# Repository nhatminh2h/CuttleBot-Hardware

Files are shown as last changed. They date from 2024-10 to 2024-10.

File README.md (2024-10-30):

# CuttleBot and FOLD Actuator Electronics Design
This repository contains the electronics design files and firmware for the CuttleBot, a biomimetic underwater robot, and its FOLD actuators. The system architecture is designed for efficient control and feedback, providing precise manipulation of the actuators for underwater mobility.

A follow up work from [Fin ray-inspired, Origami, Small Scale Actuator for Fin Manipulation in Aquatic Bioinspired Robots](https://arxiv.org/abs/2407.16821)

---

## System Overview

The CuttleBot's electronic system is divided into two key components:
1. **Main Controller**
2. **Driver and Actuator Modules (8 units)**

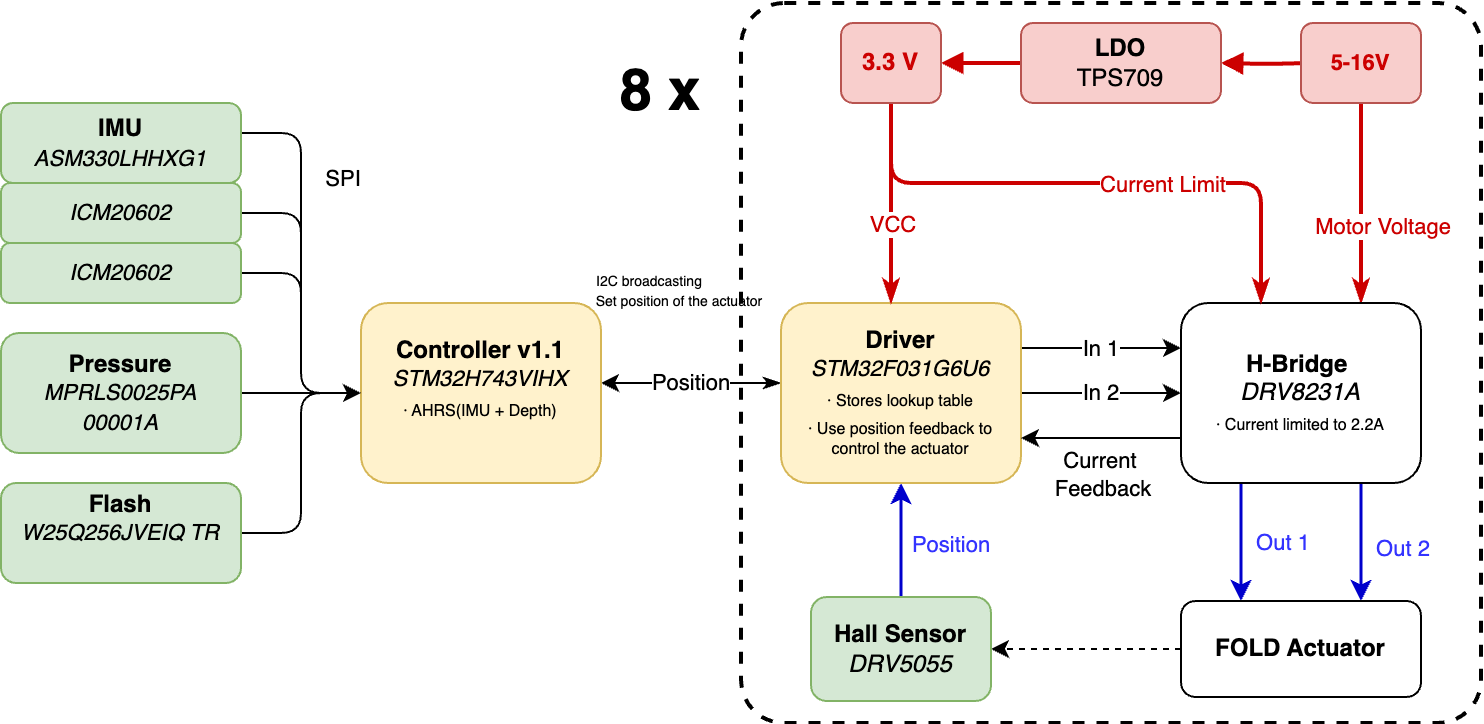
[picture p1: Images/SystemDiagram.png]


---

## Components

### Main Controller (Current version: v1.1)

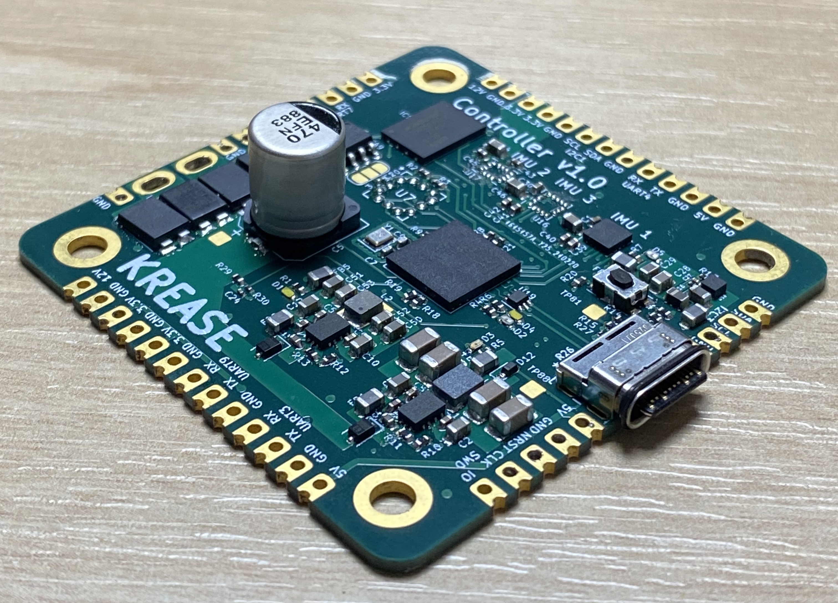
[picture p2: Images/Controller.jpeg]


- **Microcontroller**: STM32H743VHX
- **Connected Sensors**:
  - **IMU**: Three sensors (ASM330LHHXG1, ICM20602, ICM20602) are connected over SPI to provide Attitude and Heading Reference System (AHRS) data for underwater navigation.
  - **Pressure Sensor**: MPRLS0025PA 00001A, used to determine depth.
  - **Flash Memory**: W25Q256/VEIQ TR, for data storage.

The main controller (STM32H743VHX) processes data from the IMUs and the pressure sensor to calculate the robot's position and orientation. It then broadcasts the actuator position setpoints over I2C to each of the driver modules.

### Driver Module (8 units)

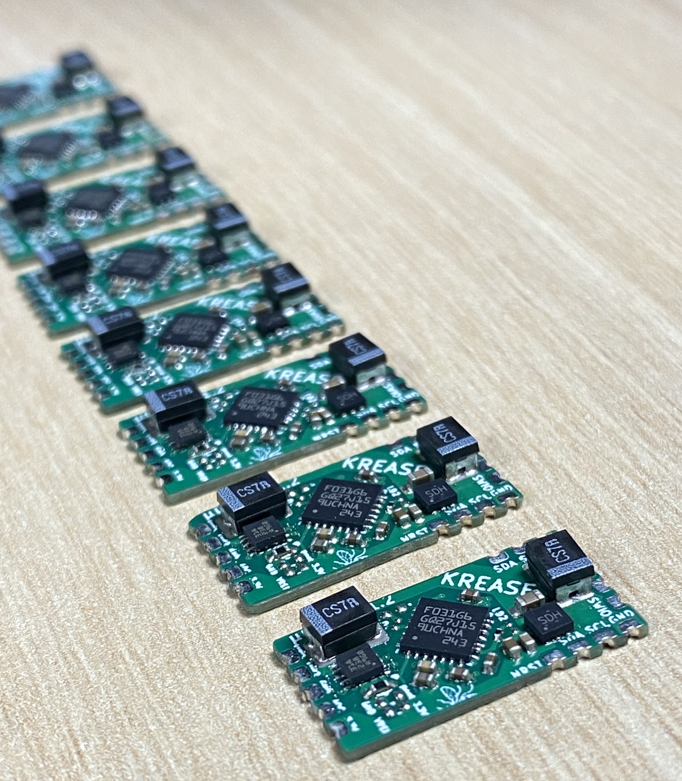
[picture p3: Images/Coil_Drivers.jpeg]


Each FOLD actuator has its own dedicated driver module, responsible for controlling the actuator's motion and maintaining position feedback. The driver module is built around the following components:

- **Microcontroller**: STM32F031G6U6
  - Stores lookup tables for position control and uses feedback from the Hall sensor to control actuator position.
  
- **Hall Sensor**: DRV5055
  - Provides position feedback to the driver, enabling precise control of actuator movement.

- **Motor Driver (H-Bridge)**: DRV8231A
  - Drives the actuator with current limiting up to 2.2A, allowing bidirectional motor control.
  - Receives control signals from the driver microcontroller.

- **Voltage Regulation**: 
  - **LDO (TPS709)** provides a stable 3.3V supply for the driver microcontroller and Hall sensor.
  - Supports a motor voltage range of 5-16V for the H-Bridge.

#### FOLD Actuator

The FOLD actuator is an origami-inspired, electromagnetically driven, tendon-driven actuator. Controlled via the H-Bridge and regulated by position feedback from the Hall sensor, the actuator provides precise biomimetic movement for underwater mobility.

---

### Power and Communication

- **Power**:
  - Each driver module includes an LDO (TPS709) to provide a stable 3.3V for the microcontroller and sensor circuits.
  - The motor voltage can range from 5-16V, which also powers the H-Bridge for actuator control.
  
- **Communication**:
  - **I2C** is used by the main controller to broadcast actuator position setpoints to each driver module.
  - **SPI** communication links the main controller to the IMUs, pressure sensor, and flash memory.

---

### Getting Started

1. **Cloning the Repository**:
   ```bash
   git clone https://github.com/[username]/cuttlebot-electronics.git

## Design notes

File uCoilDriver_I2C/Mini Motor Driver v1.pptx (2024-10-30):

## Mini Motor Driver v1.0 – Overview

- Nominal input voltage: 5-18V

Gus Zhang <cheng.zhang@manchester.ac.uk> , Aug 2023

Connector pitch: 1.27 mm

Left Connector (FPC)
Motor Drive Out 1
Motor Drive Out 2
GND – Hall Sensor
+3V3 – Hall Sensor
Out – Hall Sensor

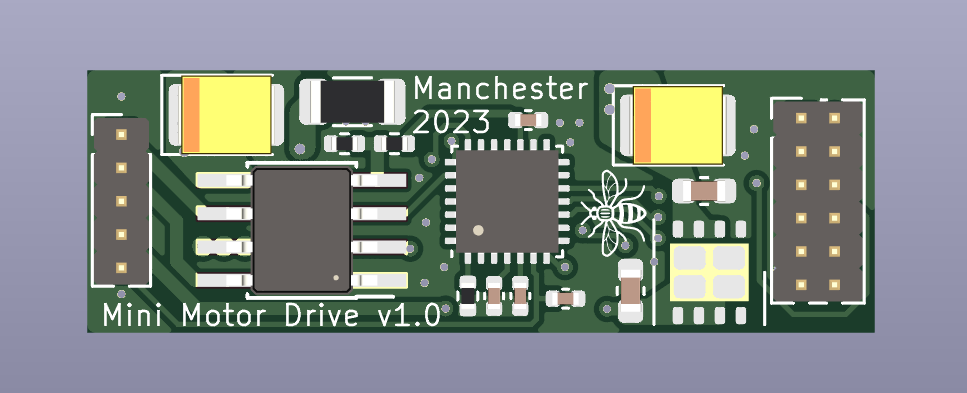
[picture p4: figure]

3cm

Right Connector (MB)
+12V | +12V
GND | GND
SPI_MOSI | UART_TX
SPI_SCK | UART_RX
SPI_NSS | SWDIO
NRST | SWCLK

1cm

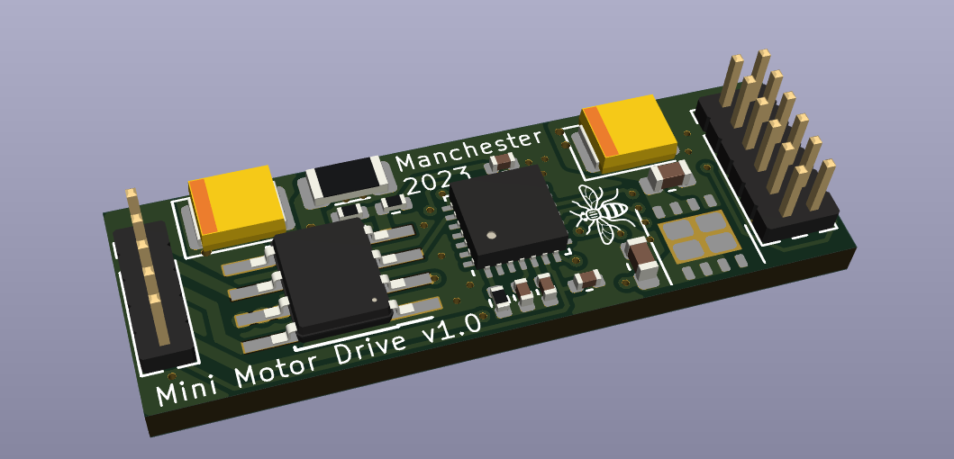
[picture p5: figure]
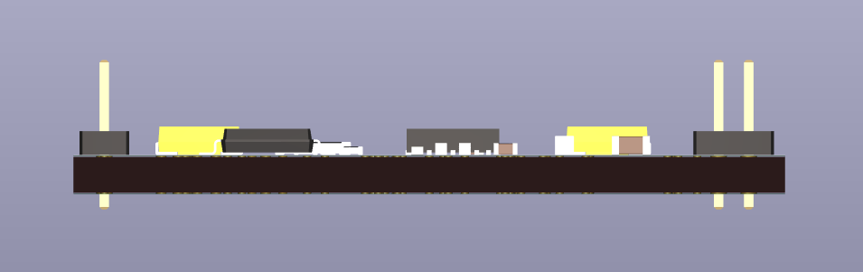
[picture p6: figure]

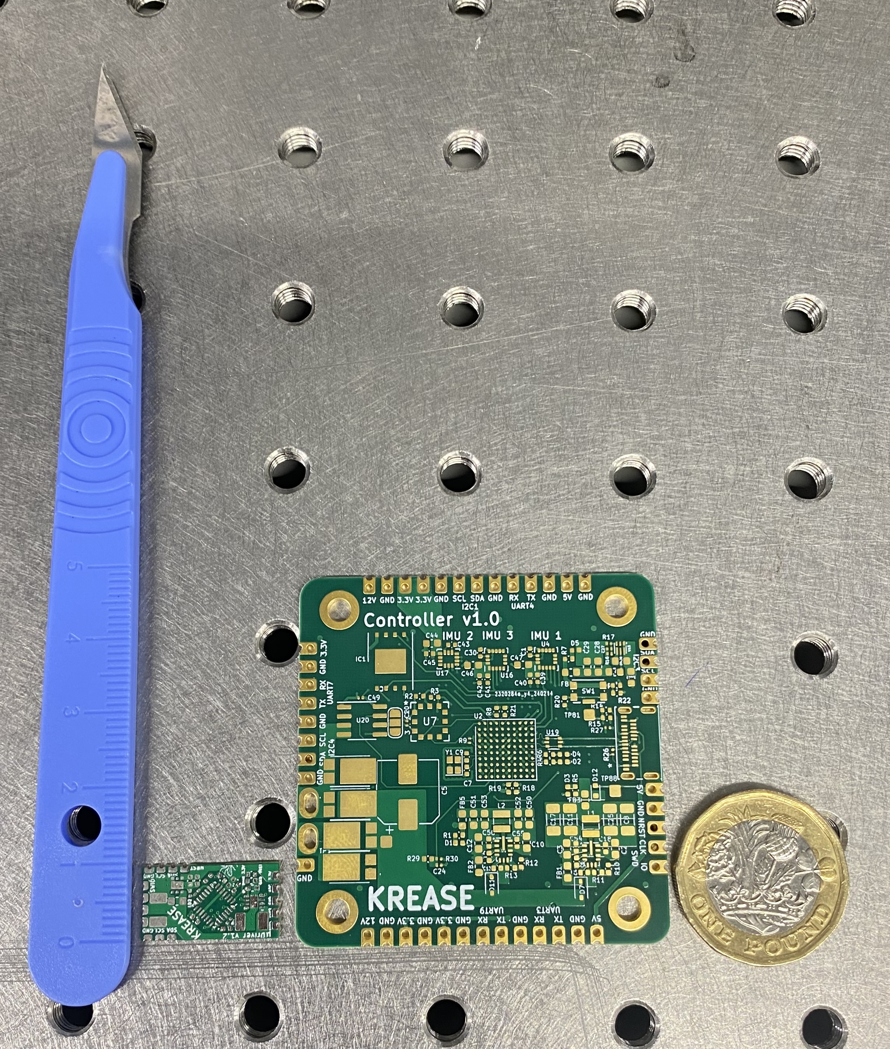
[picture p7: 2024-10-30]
Images/PCBs.jpeg

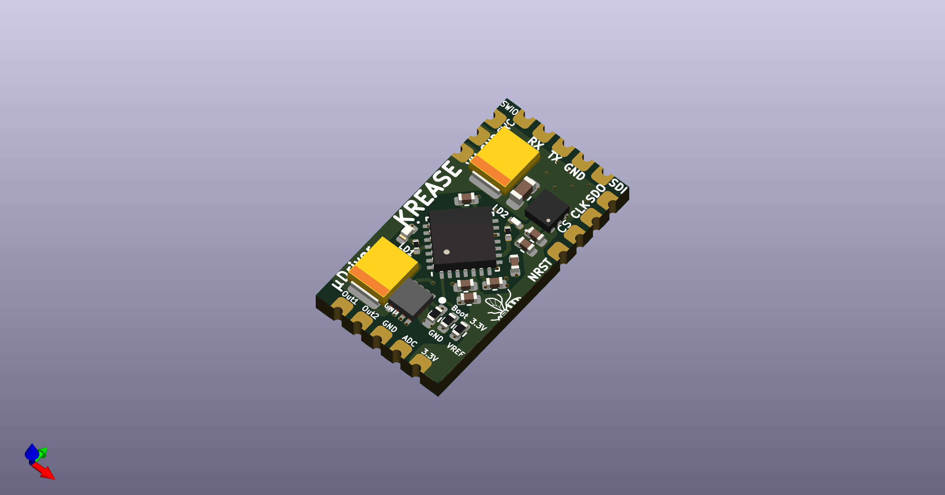
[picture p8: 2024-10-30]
uCoilDriver_I2C/uCoilDriver_I2C.png

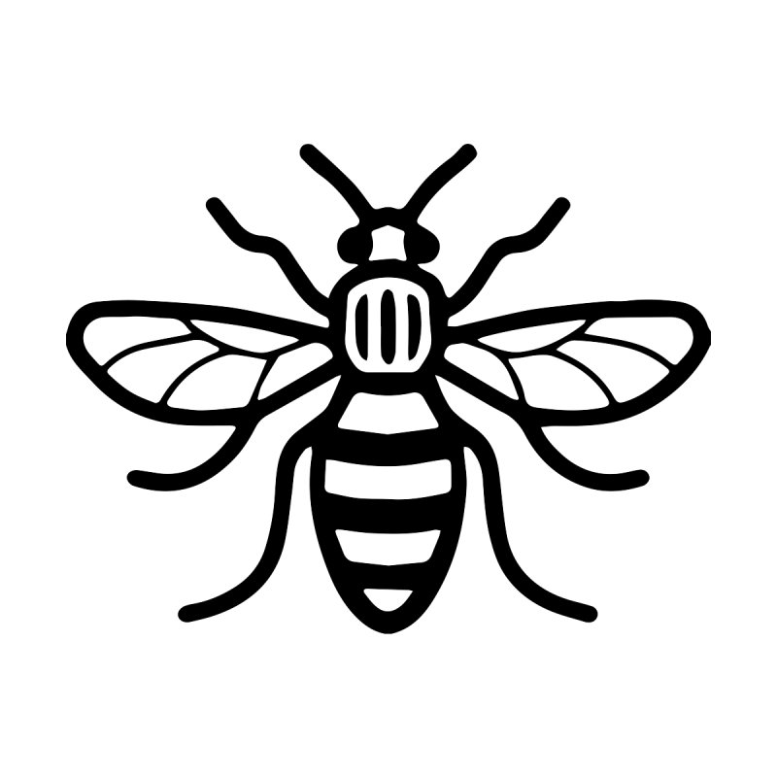
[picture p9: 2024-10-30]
uCoilDriver_I2C/shirt-1535906197-74bee4203cf0f0dfc7fb7f64e88a406c.jpeg

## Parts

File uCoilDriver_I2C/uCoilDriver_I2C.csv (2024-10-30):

Reference | Value | Footprint | Datasheet | Height | JLCPCB Part # | JLCPCB Part# | Manufacturer_Name | Manufacturer_Part_Number | Mouser Part Number | Mouser Price/Stock | Qty
C1, C6, C8 | 100n | Capacitor_SMD:C_0402_1005Metric | ~ |  |  |  |  |  |  |  | 3
C2 | 1 uF | Capacitor_SMD:C_0603_1608Metric | ~ |  |  |  |  |  |  |  | 1
C3 | 2.2 uF | Capacitor_SMD:C_0402_1005Metric | ~ |  |  | C2999759 |  |  |  |  | 1
C4, C7 | 47u | Capacitor_Tantalum_SMD:CP_EIA-3528-12_Kemet-T | ~ |  |  |  |  |  |  |  | 2
C5 | 4.7 uF | Capacitor_SMD:C_0402_1005Metric | ~ |  |  | C2999759 |  |  |  |  | 1
C11 | 10n | Capacitor_SMD:C_0402_1005Metric | ~ |  |  | C272878 |  |  |  |  | 1
C12 | 1 uF | Capacitor_SMD:C_0402_1005Metric | ~ |  |  | C528974 |  |  |  |  | 1
D1 | BLUE LED | LED_SMD:LED_0402_1005Metric | ~ |  |  |  |  |  |  |  | 1
D2 | BLUE LED | LED_SMD:LED_0201_0603Metric | ~ |  |  |  |  |  |  |  | 1
R1 | 100k | Resistor_SMD:R_0402_1005Metric | ~ |  |  |  |  |  |  |  | 1
R2 | 0 | Resistor_SMD:R_0402_1005Metric | ~ |  |  |  |  |  |  |  | 1
R3, R5 | 1k5 | Resistor_SMD:R_0201_0603Metric | ~ |  |  |  |  |  |  |  | 2
R4 | 1k5 | Resistor_SMD:R_0402_1005Metric_Pad0.72x0.64mm_HandSolder | ~ |  |  |  |  |  |  |  | 1
TP1-TP3, TP6-TP8, TP11-TP17 | Pad | Connector:Castellated_Pad_1x2mm | ~ |  |  |  |  |  |  |  | 13
U1 | DRV8231ADSGR | Package_SON:SON50P200X200X80-9N | https://www.ti.com/lit/ds/symlink/drv8231a.pdf?ts=1648534030931 | 0.8 |  |  | Texas Instruments | DRV8231ADSGR | 595-DRV8231ADSGR | https://www.mouser.co.uk/ProductDetail/Texas-Instruments/DRV8231ADSGR?qs=Rp5uXu7WBW%252BKZGX8zD3MhQ%3D%3D | 1
U2 | STM32F031G6Ux | Package_DFN_QFN:QFN-28_4x4mm_P0.5mm | https://www.st.com/resource/en/datasheet/stm32f031g6.pdf |  |  |  |  |  |  |  | 1
U3 | TPS709 | Package_SON:WSON-6-1EP_2x2mm_P0.65mm_EP1x1.6mm | https://www.ti.com/lit/ds/symlink/tps709.pdf |  |  | C2872343 |  |  |  |  | 1

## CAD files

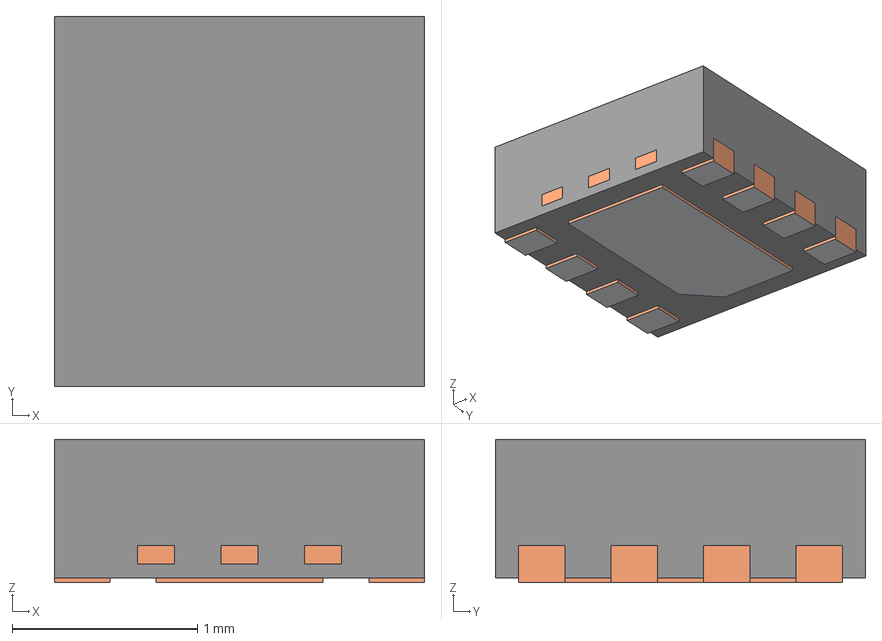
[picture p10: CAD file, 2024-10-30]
uCoilDriver_I2C/LIB_DRV8231ADSGR/DRV8231ADSGR.stp
2.00 x 2.00 x 0.775 mm
BODY-SON
FRAME-DSG0008A
PIN1-ID

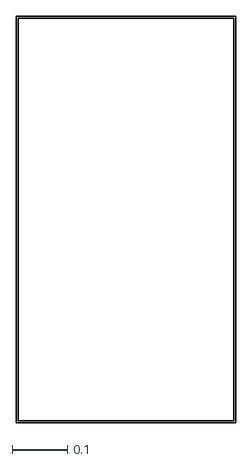
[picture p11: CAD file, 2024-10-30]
uCoilDriver_I2C/uCoilDriver_I2C-Edge_Cuts.dxf
0.398 x 0.736

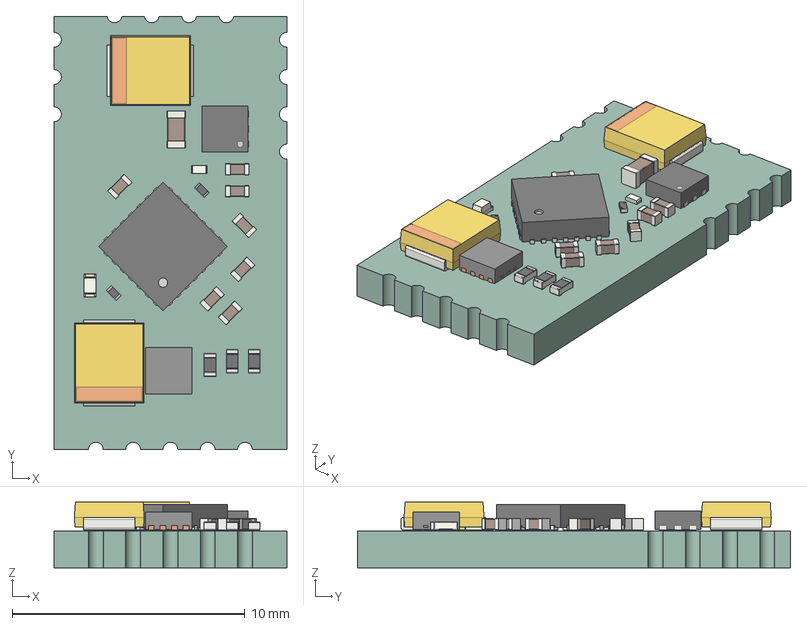
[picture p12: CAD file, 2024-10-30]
uCoilDriver_I2C/uCoilDriver_I2C.step
10.0 x 18.6 x 2.83 mm
uCoilDriver_I2C PCB

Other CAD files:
uCoilDriver_I2C/uCoilDriver_I2C-F_Mask.dxf

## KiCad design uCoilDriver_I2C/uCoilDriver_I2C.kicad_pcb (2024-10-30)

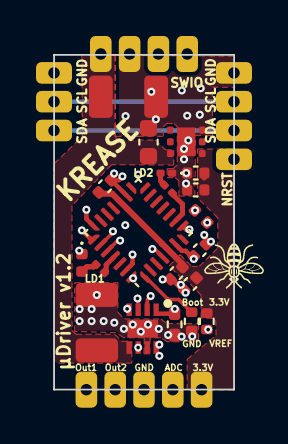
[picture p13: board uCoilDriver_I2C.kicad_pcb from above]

Board: 4 copper layers, 10.0 x 18.6 mm, 33 parts (0 on the bottom side), 20 nets.

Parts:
C1, C6, C8: 100n; C_0402_1005Metric
C2: 1 uF; C_0603_1608Metric
C3: 2.2 uF; C_0402_1005Metric
C4, C7: 47u; CP_EIA-3528-12_Kemet-T
C5: 4.7 uF; C_0402_1005Metric
C11: 10n; C_0402_1005Metric
C12: 1 uF; C_0402_1005Metric
D1: BLUE LED; LED_0402_1005Metric
D2: BLUE LED; LED_0201_0603Metric
R1: 100k; R_0402_1005Metric
R2: 0; R_0402_1005Metric
R3, R5: 1k5; R_0201_0603Metric
R4: 1k5; R_0402_1005Metric_Pad0.72x0.64mm_HandSolder
TP1, TP2, TP3, TP6, TP7, TP8, TP11, TP12, TP13, TP14, TP15, TP16, TP17: Pad; Castellated_Pad_1x2mm
U1: DRV8231ADSGR; SON50P200X200X80-9N
U2: STM32F031G6Ux; QFN-28_4x4mm_P0.5mm
U3: TPS709; WSON-6-1EP_2x2mm_P0.65mm_EP1x1.6mm

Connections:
+3.3V: C3.1, C5.1, C6.1, C11.1, C12.1, R2.2, TP16.1, U2.5 (VDDA), U2.17 (VDD), U3.1 (OUT)
+12V: C2.1, C4.1, C7.1, TP1.1, U1.5 (VM), U3.6 (IN)
/ADC_IN: C8.1, TP17.1, U2.6 (PA0)
/I2C1_SCL: TP8.1, U2.27 (PB6)
/I2C1_SDA: TP7.1, U2.28 (PB7)
/NRST: C1.1, TP6.1, U2.4 (NRST)
/OUT1: TP13.1, U1.6 (OUT1)
/OUT2: TP14.1, U1.8 (OUT2)
/PA2_IPROPI: R4.2, U1.1 (IPROPI), U2.8 (PA2)
/SWCLK: TP3.1, U2.22 (PA14)
/SWDIO: TP12.1, U2.21 (PA13)
/TIM2_CH1: U1.3 (IN1), U2.23 (PA15)
/TIM2_CH2: U1.2 (IN2), U2.24 (PB3)
GND: C1.2, C2.2, C3.2, C4.2, C5.2, C6.2, C7.2, C8.2, C11.2, C12.2, D1.1 (K), D2.1 (K), R1.1, R4.1, TP2.1, TP11.1, TP15.1, U1.7 (GND_1), U1.9 (GND_2), U2.16 (VSS), U3.3 (GND), U3.7 (GND)
unnamed: D1.2 (A), R3.1
unnamed: D2.2 (A), R5.1
unnamed: R2.1, U1.4 (VREF)
unnamed: R1.2, U2.1 (BOOT0)
unnamed: R5.2, U2.9 (PA3)
unnamed: R3.2, U2.25 (PB4)
